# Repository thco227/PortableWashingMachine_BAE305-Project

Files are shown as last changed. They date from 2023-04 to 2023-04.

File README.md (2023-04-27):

# PortableWashingMachine_BAE305-Project
The following report contains the documentation of the construction of a portable washing machine for the class BAE 305. The members of this team were Maggie Barnes, Tiffany Coogle, Elyssa Roberts, and Hunter Walters.

## Summary
The goal of our project was to create a portable washing machine. The portable washing machine is applicable for situations in which the user has only a few small items of clothing to wash, and does not want to use a full size washing machine for them. Because of this, the portable washing machine that was created is most suitable for items such as socks, underwear, etc. The portable washing machine body is made from a 2 gallon bucket, and contains two pumps, a valve, a motor, and a 3D printed impeller. An Arduino RedBoard was used to control the operation of each component of the washing machine. The washing machine has three cycles: 1, 2, and 3 minutes, which each fill and drain twice to wash the clothes, remove the dirty water, then rinse. The user can select the desired cycle by inputting their selection into the serial monitor of the computer connected to the RedBoard. Then, when the user is ready, a switch can be used to start the cycle. At the end of the cycle, a buzzer beeps to notify the user to remove their clothes from the washing machine. Should the user need to stop the cycle before the specified duration, the switch can be used to stop the cycle midway. This project was initiated in January 2023 and progress was tracked using the Scrum project development method. The complete project was presented for assessment on April 20th, 2023, and all features on our project backlog were demonstrated successfully.



## Design Description 

### Materials
* 4 V23234-B1001-X004 Plug-in Mini ISO Relays
* 4 relay bases
* Jumper wires
* 3 TIP 31C Transistors
* 3 10k ohm resistors
* Arduino RedBoard
* Computer with Arduino IDE downloaded
* 1 Piezo Buzzer
* 1 Button
* 2 B07X9L5RNS HiLetgo DC Brushless Water Pumps (240L/min)
* 1 B08KS6FMC7 Gredia N/C DC Solenoid Valve
* 3/8" od. tubing
* LS-00086 OSEPP Electronics LTD DC Motor
* Global Specialties 100W Triple Output Switching DC Power Supply
* Female and Male Spade Connectors
* Crimper/wire stripper
* 2 Gallon Bucket with Lid
* 3D Printed Impeller
* 3D Printed Shaft Connector
* 1" od. PVC Pipe
* Hand Saw
* Kroger 1 Gallon Chocolate Ice Cream Bucket
* 1 set of Alligator Probes

### Design

#### Physical Design
When first creating the design for the washing machine, a five gallon bucket was the selected size for the unit. However, after calculating the torque needed to move that much water plus clothing and considering the voltage requirements and prices, a size reevaluation was necessary. A five gallon bucket half full of water was estimated at about 8 pounds without the weight of clothing. With a half foot of diameter estimated, around 4 lb-ft of torque would be needed at the minimum. The motors rated at this torque were very expensive and often required higher voltages. In the end, a 2 gallon bucket was decided on, with the intention to not fill it completely. Based on the size adjustment, a motor was chosen. The LS-00086 DC motor was chosen due to its low price, low voltage, and torque rating of 2.18 lb.-ft. The B07X9L5RNS brushless DC water pumps were chosen for their pumping capacity (240 L/min), low price, and low voltage/power consumption. Two were purchased: one to pump water in and one to empty the reservoir. In addition to these pumps, a B08KS6FMC7 Gredia normally closed DC solenoid valve was chosen to keep the unprimed outlet pump from continuing to send water into the drain.

Based on the size adjustment, a motor was chosen. The LS-00086 DC motor was chosen due to its low price, low voltage, and torque rating of 2.18 lb.-ft. The B07X9L5RNS brushless DC water pumps were chosen for their pumping capacity (240 L/min), low price, and low voltage/power consumption. Two were purchased: one to pump water in and one to empty the reservoir. In addition to these pumps, a B08KS6FMC7 Gredia normally closed DC solenoid valve was chosen to keep the unprimed outlet pump from continuing to send water into the drain.

#### Circuit Design
When designing the washing machine, an important factor was being able to control the operation of the pumps, motor, and valve, which all operated at 12 volts DC. This voltage could not be supplied from the RedBoard alone, so relays were used to switch them on and off. The components of the washing machine were connected to the switch connected terminals on the relay. A 12 volt supply was connected to these terminals as well. When the relay was turned on, the switch would close, allowing the 12 volts to flow to ground, and subsequently turning on the desired component. 

To turn the relay on and off, a controllable signal was needed on the non-switch connected terminals. However, the current needed to turn on the relay was calculated to be _ mA, which was too high for the RedBoard to produce. To achieve the desired current, transistors were used. The TIP31C models were used in the circuit. Four digital output pins (7, 8,12, and 13) from the RedBoard were connected to the bases of the transistors. A 12 volt supply was connected to the collector on the transistor. The emitter was connected to the relay. When the RedBoard sent out a 5 volt signal to the transistor, the 12 volts attached to the transistor would be allowed to flow through the relay to ground. This higher voltage was able to produce enough current to trigger the relay.

The design of the circuit also included a piezo buzzer and a switch. They were connected to the RedBoard via pins 5 and 2 respectively. When pin 5 sent out a signal, the buzzer would play a tone. Pin 2, which was connected to the switch, was set to input pullup mode. This meant that the pin would read zero until the switch was moved, then it would read low. The input pullup resistor mode was used to prevent floating values.  

To help make the schematic easier to read, the wires leading to ground are highlighted in red, the wires connected to power are highlighted in green, and the wires connected to a pin are various colors of blue.



#### Code

The code that operated the circuit was created in Arduino IDE and is explained below. First, the pins were set as constant integer variables as shown below.
```c
const int SpeakerPin = 5;

const int MotorPin = 7;

const int DrainPin = 8;

const int PumpPin = 12;

const int ValvePin = 11;

const int OnOffPin = 2;
```
The variable "CycleType" was initialized as a string so it could hold other strings. This was essential to allow the user's input to be read correctly.
```c
String CycleType;
```
The following variables set the time to run each component of the washing machine. A "long" variable type, which allows numbers from -2,147,483,648 to 2,147,483,647 to be assigned to it, was used. This allowed for a higher level of variability in the cycles. The times could be set to larger numbers than was possible with an integer variable, which only went from -32,768 to 32,767.
```c
long FillTime;

long SpinTime;

long DrainTime;

long ValveTime;
```
In the setup loop, the all pinmodes except the switch pin were set to output. These pins needed to output HIGH to activate the transistors.
```c
void setup() {

pinMode(SpeakerPin, OUTPUT);

pinMode(MotorPin, OUTPUT);

pinMode(DrainPin, OUTPUT);

pinMode(PumpPin, OUTPUT);

pinMode(ValvePin, OUTPUT);
```
The switch pin was set to input pullup. This allowed the switch to ground a signal when connected.
```c
pinMode(OnOffPin, INPUT_PULLUP);
```
In this loop, serial connection was created by using the Serial.begin command and setting the baud rate to 9600.
```c
Serial.begin(9600);
```
Finally, the setup loop was concluded by displaying a message to prompt user input to choose a cycle type and instructing the user how to use the switch.
```c
Serial.println("Push switch towards resistor side before inputing cycle type if ready to start cycle. 
During the cycle push the switch away from the resistor if you would like the cycle to end.");

Serial.println("Choose cycle: Light, Normal, Heavy");

Serial.println("L = Light, N = Normal, H = Heavy");
}
```
The main loop was comprised of many if and else statements. The blanketing if statement told the program to start if the user input something into the serial monitor. 
```c
void loop() 
{
if (Serial.available() > 0)
```
The string variable "CycleType" stored the input until "\n" was found, which equated to the user pressing the enter key. Depending on the user input, three different if or else if statements could be triggered. These three loops had varying messages and times to correspond with the cycle type. The light cycle is shown below, however the normal and heavy cycles have the exact same code, except with the time variables set to different times and the messages displaying the corresponding cycle. Note that the times are given in milliseconds.
```c
CycleType = Serial.readStringUntil('\n');

if (CycleType == "L")

Serial.print("You have chosen LIGHT.");

FillTime = 15000;

DrainTime = 30000;

SpinTime = 5000;
```
To easily adjust and call upon the major actions of the washing machine, functions were created. Fill, drain, valve, and motor functions were comprised of turning the corresponding pin to high, delaying for a set time, and then turning the pin to low. By setting the time in each function to a variable, the times for each cycle type could be easily adjusted. Each cycle type redefined the times for each function to allow to customize the intensity. The fill function is shown below, however the other functions follow a similar outline, with different pins being set to HIGH.

```c
void fill(){

  digitalWrite(MotorPin, LOW);
  
  digitalWrite(ValvePin, LOW);
  
  digitalWrite(DrainPin, LOW);

  digitalWrite(PumpPin, HIGH);
  
  delay(FillTime);

  digitalWrite(PumpPin, LOW); }
  ```

In each cycle, after the times were defined, the same sequence code would run. The sequence called on various functions created to fill, spin, drain, and turn the valve on and off. Before inputing a cycle type into the serial monitor, the user would be prompted to turn the switch toward the resistor on the breadboard if they were ready to start the cycle. With the switch toward the resistor, the pin would read LOW. When the switch was pressed away from the resistor, the pin would read zero. The code used this to create a system in which the cycle could be stopped in the middle. This was accomplished by putting an if statement before each step of the cycle. When the switch was pushed toward the resistor, it would read LOW, and would allow the code to run. If pressed away, the pin would read zero, and the code would stop because the conditions would not be fulfilled.
```c
if (digitalRead(OnOffPin)==LOW) fill();

if (digitalRead(OnOffPin)==LOW) spin();

if (digitalRead(OnOffPin)==LOW) drain();

if (digitalRead(OnOffPin)==LOW) fill();
```
A function for the beep at the end of the cycle was also created, which included the tone command so the pin, frequency, and duration could be selected. This function was not put within an if statement on the condition of the switch, so the user would know if their cycle had ended had they decided to end it midway.

```c
void StopBeep() {
  digitalWrite(MotorPin, LOW);
  
  digitalWrite(ValvePin, LOW);
  
  digitalWrite(DrainPin, LOW);
  
  digitalWrite(PumpPin, LOW);

  tone(SpeakerPin, 500, 1000);
}
```

#### 3D Printing Design
For the inner workings of the machine, we researched actual appliances. Commercially available washing machines most often employ one of two washing methods: agitation or impeller washing. In an agitation washing machine, a central shaft with vanes rotates to spin clothes in water and wash them. An impeller is a low disc with fins that sits at the bottom of the basket, and impeller washing uses this structure to wash clothes. The design takes advantage of the friction generated between the articles of clothing to wash them and uses less water than an agitation machine does. For our small scale machine, we wanted to optimize our water use, so the impeller design was the ideal choice. When we took into consideration the materials we would be using, we realized it would be far easier to 3D print an impeller than a central agitator.

Our impeller design is simple: it's a flat disc that rises in the center to form a low cone. This center is hollow to allow our central shaft, a PVC pipe with an outer diameter of approximately 1 in, to be inserted. From the center cone, eight identical vanes protrude, lofting down to meet the edge of the disc. Commercial impellers tend to have six of these vanes, but we chose to use either for a more sturdy impeller, as, at the time of designing this part, we were unsure how much stress the impeller would be under. Future iterations of this project should test different impeller designs. The eight-vaned impeller part file is shown below.

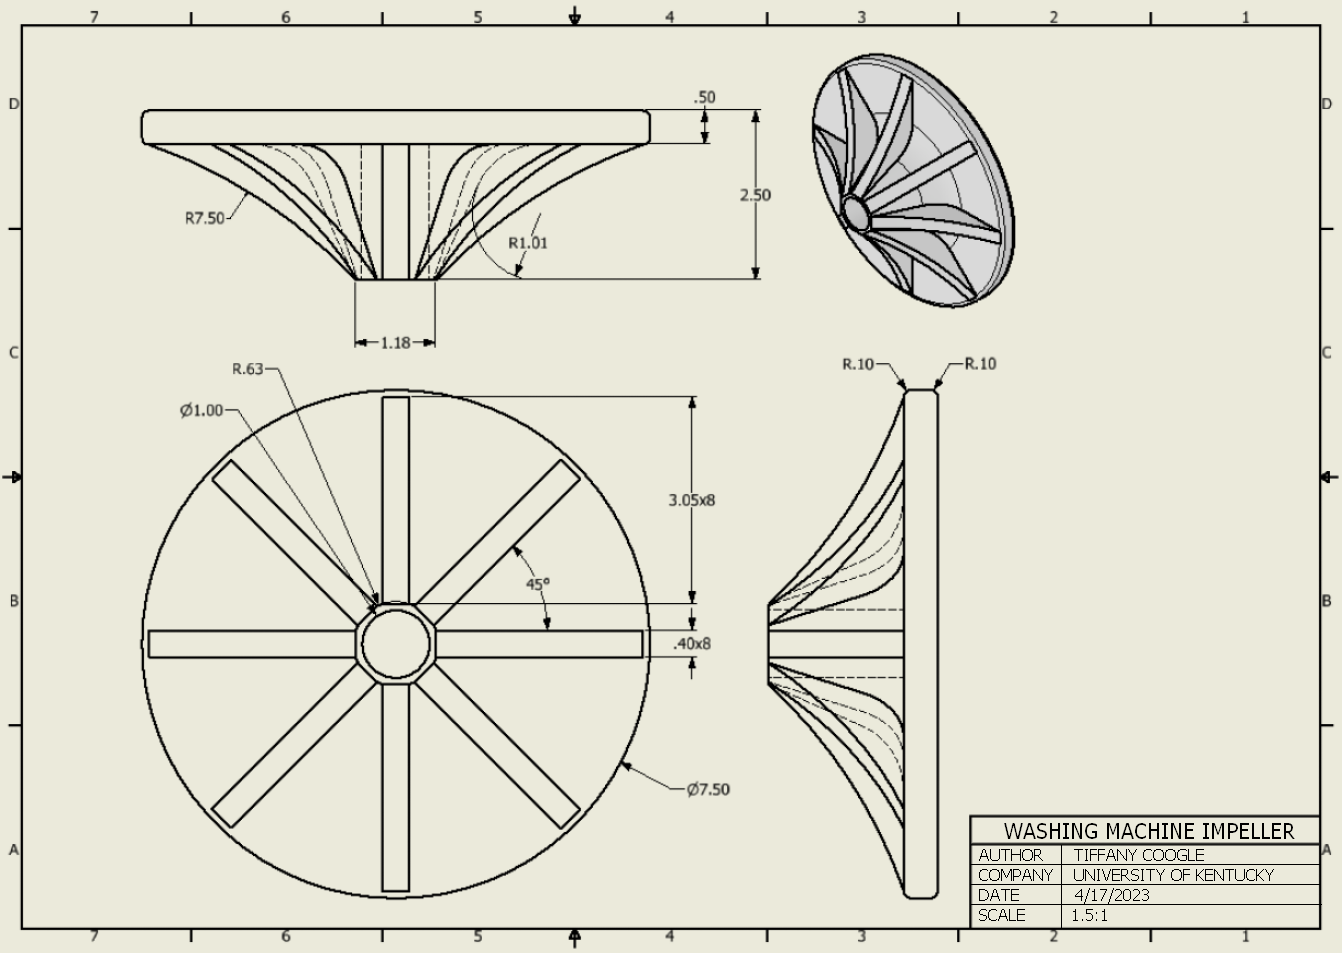
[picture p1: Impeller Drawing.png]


To create this part, we used the 3D printers available at the Innovation Center at the University of Kentucky. The printer used was the Prusa Mini+, printing with Inland 1.75mm PLA filament. This printer's print bed is a 7 in square, which is just smaller than the impeller's diameter of 7.5 in. To use the Prusa Mini+, we cut our impeller file into four identical parts, as in the drawing file below. These four parts each had a mass of 40.01 grams, resulting in a total combined mass of 164.04 grams. 

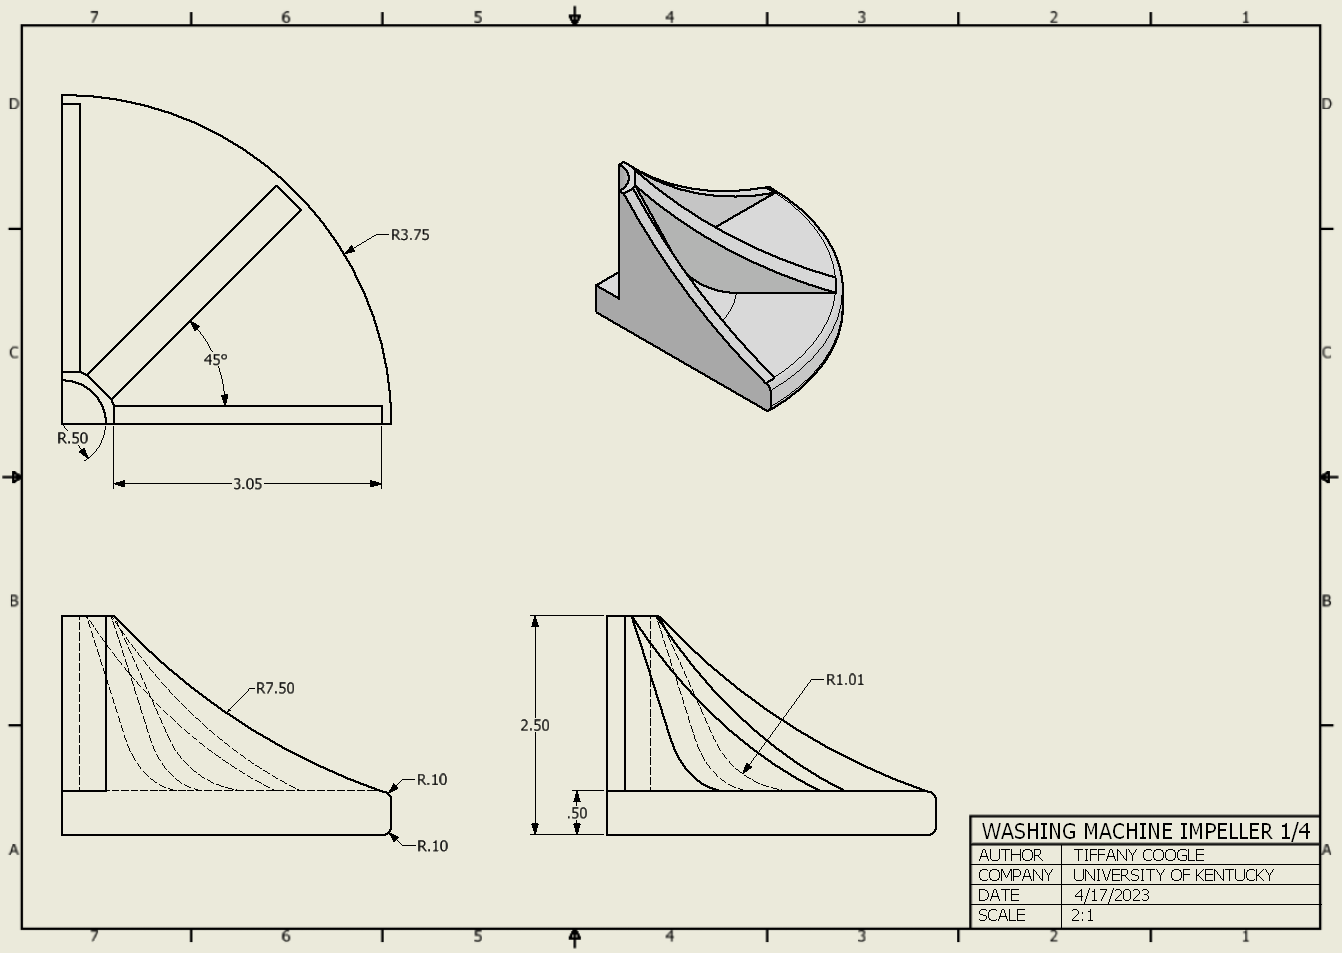
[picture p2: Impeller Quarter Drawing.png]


Once these were printed, the triangular faces were glued together using E6000 industrial adhesive to form the full impeller, as shown in this photograph.

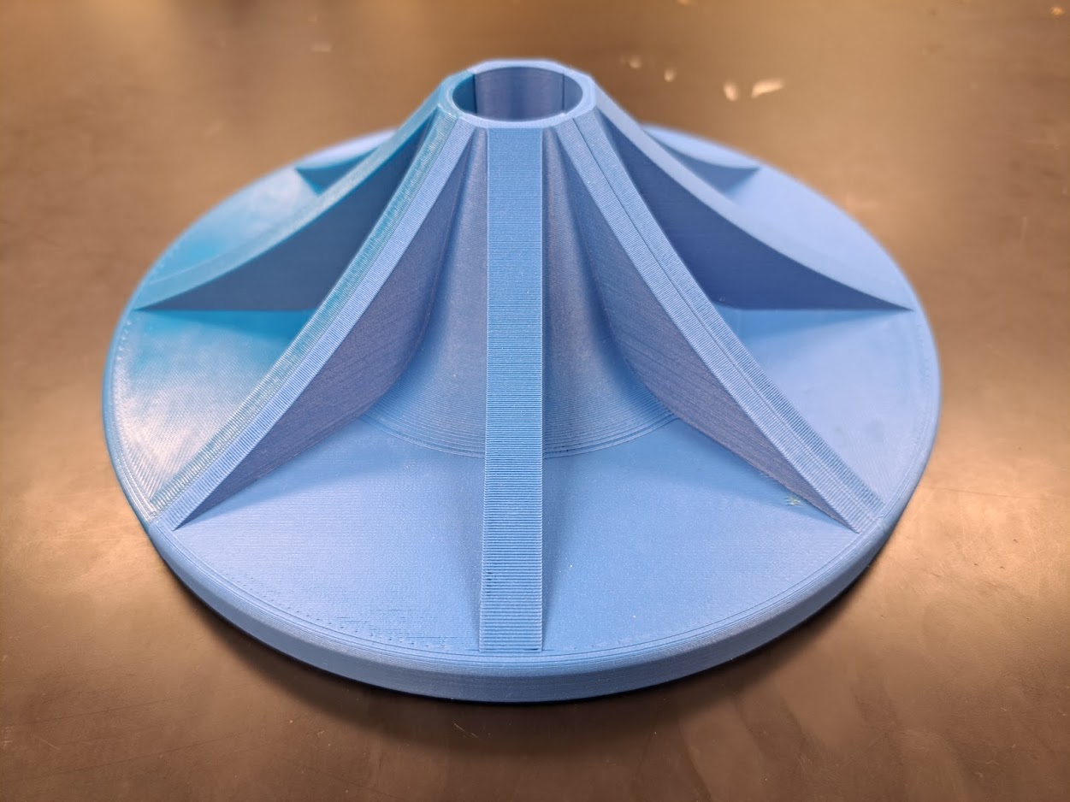
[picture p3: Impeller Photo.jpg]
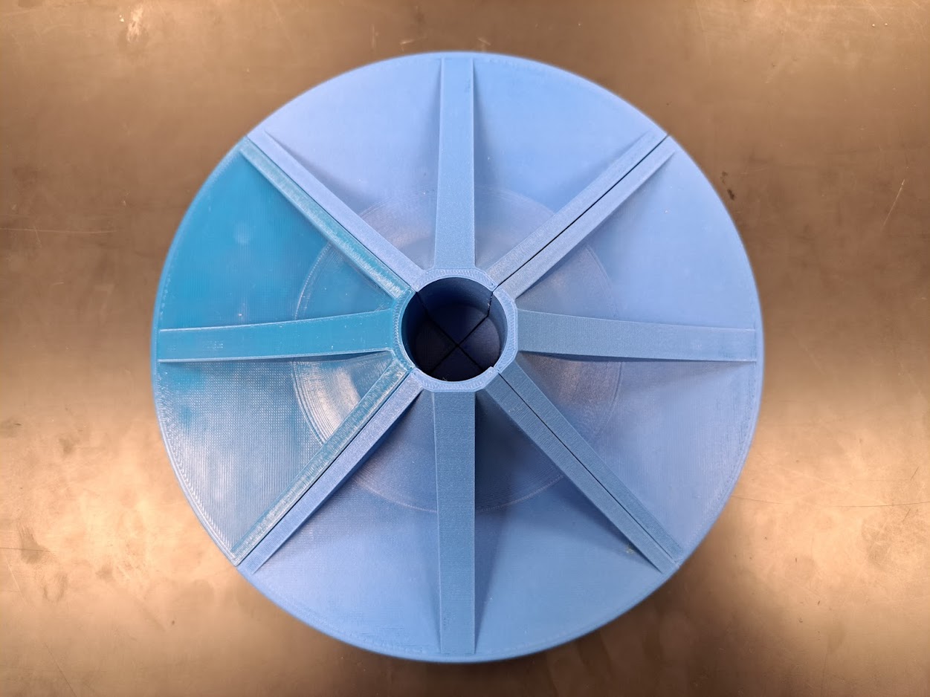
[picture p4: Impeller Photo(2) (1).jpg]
 

Another key component of the physical washing system is the motor mount. As mentioned previously, we chose to use a section of PVC pipe as a central shaft that would connect our impeller to the motor. To rotate this shaft from the motor key, we designed a fitting for the end of the pipe that has a hole to insert the motor shaft. This part was printed using the Prusa Mini+, with Inland 1.75mm PLA. The total mass of the print was 13.18 grams. The images show our drawing file and photos of the final print.

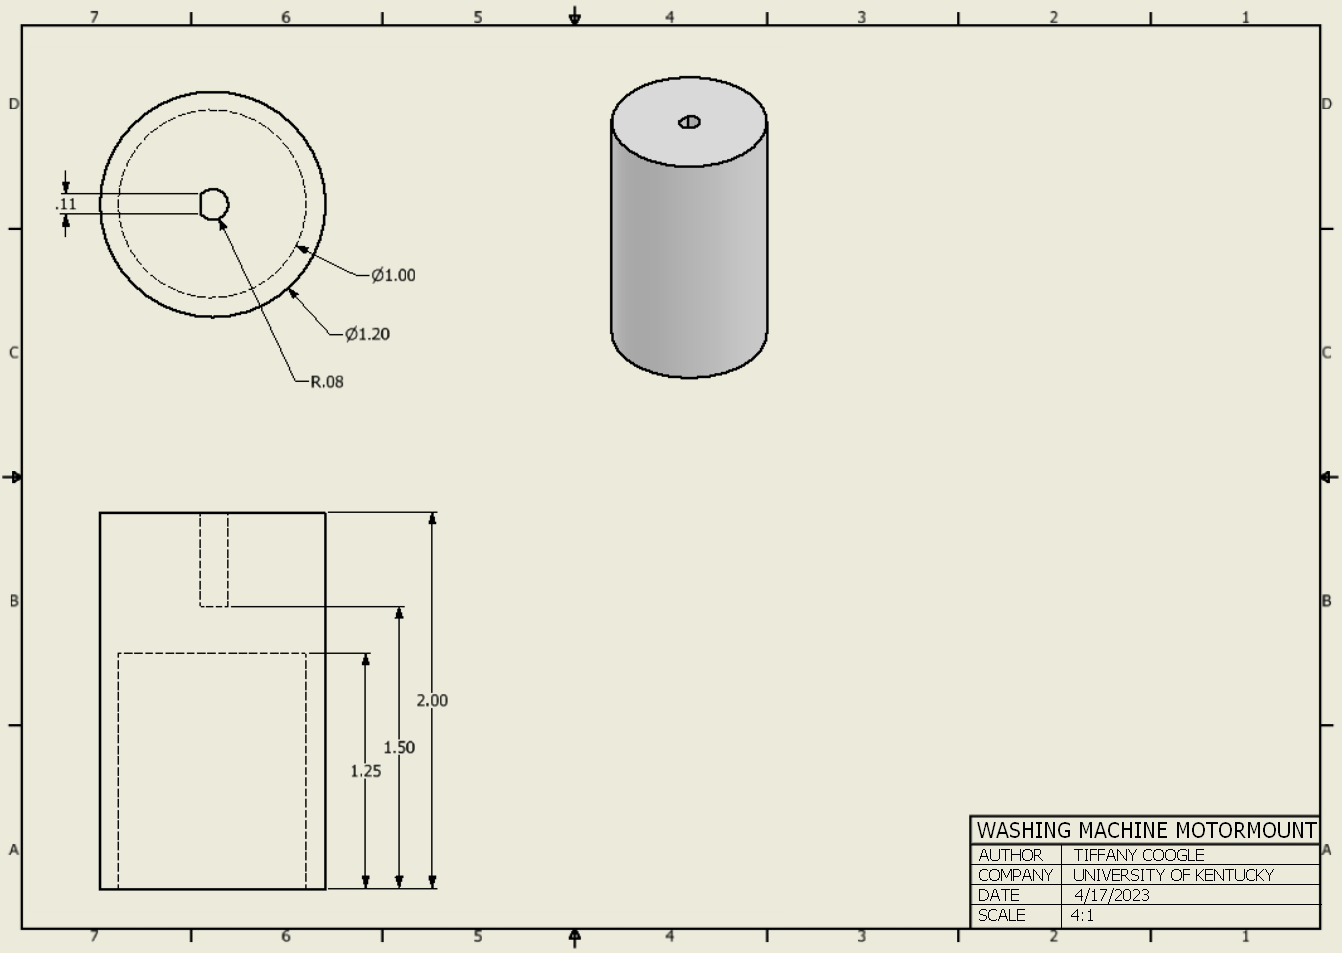
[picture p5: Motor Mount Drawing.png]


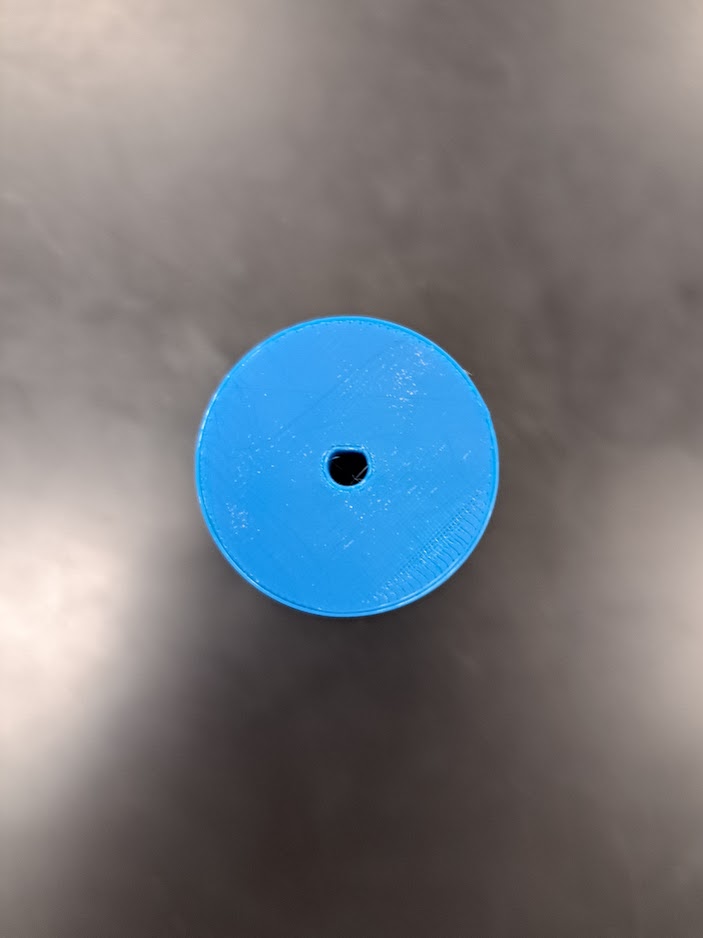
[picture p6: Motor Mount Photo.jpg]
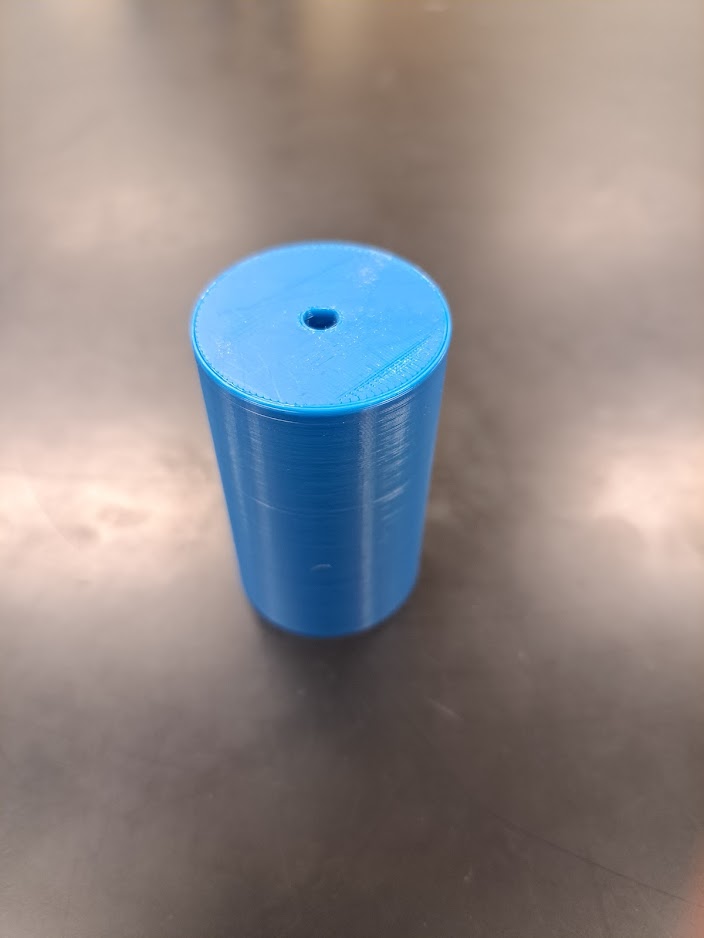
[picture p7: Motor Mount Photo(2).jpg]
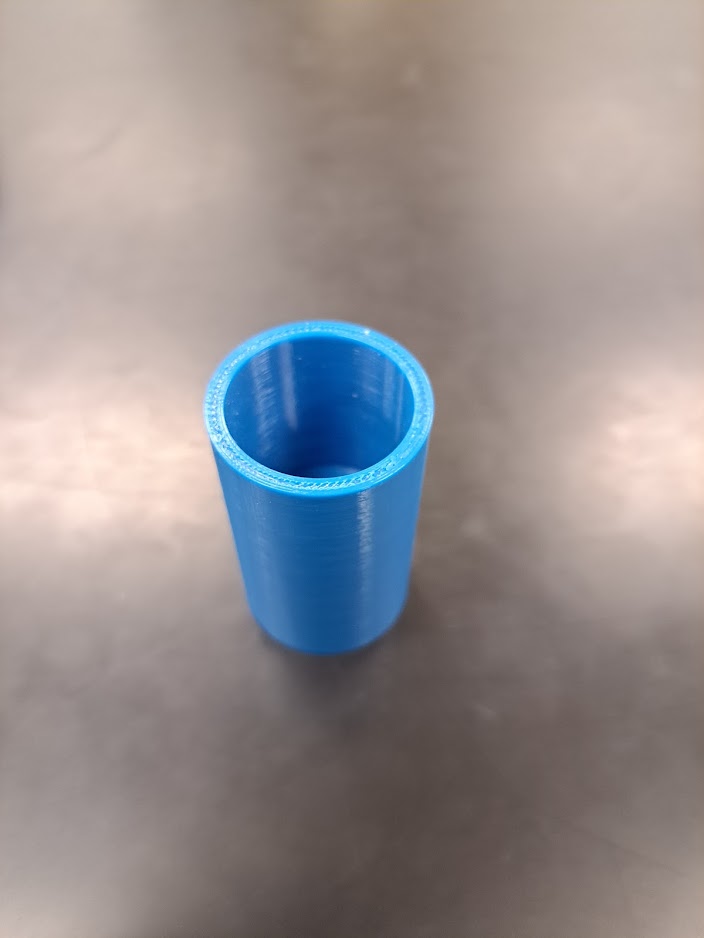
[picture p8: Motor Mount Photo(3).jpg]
  

#### Laser Cut Design

The initial plan for the stand that would hold the bucket up was to 3D print. With the design having a diameter right above 9 inches, an industrial size printer would have been needed to perform the print. Then considering a new way to print smaller pieces and glue them together, the cost and time to do so was still not reasonable. The final solution was to laser cut 4 (dimensions) pieces, 1 base piece that was (dimensions) with a circle cut out in the middle, and 8 (dimensions) to create legs so that the bucket would be lifted. The circle cut out of the bottom and the legs being added so the bucket was 4 inches off the surface, was to supply room for the motor to be mounted. These components were laser cut from a 11.5 x 23.5 x .25 inch thick piece of wood. When laser cut, divots were added to the edges of the components to help them be glued together with more ease and stability. Gorilla wood glue was used to hold the pieces together.
 
!!!!!PICTURE OF PEICES LASER CUT WITH LABELED DIMENSIONS!!!!!

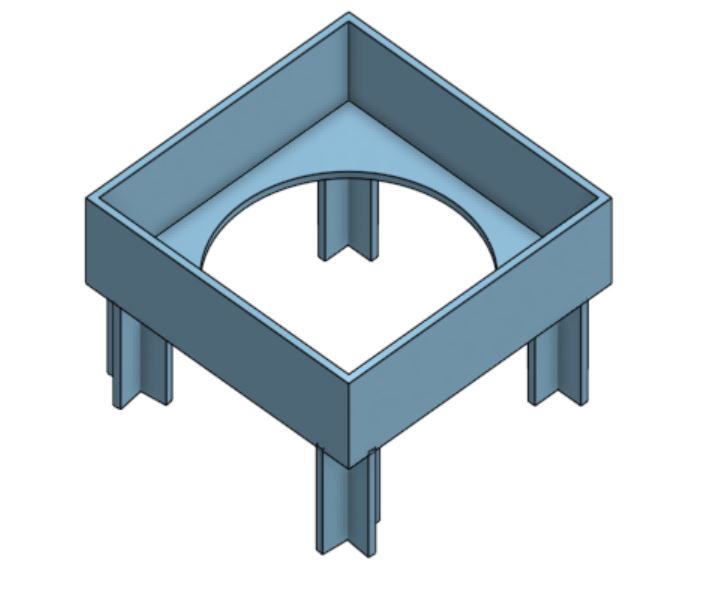
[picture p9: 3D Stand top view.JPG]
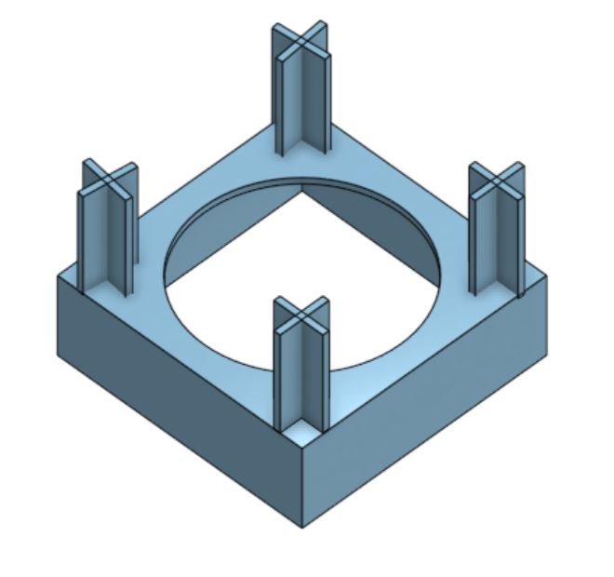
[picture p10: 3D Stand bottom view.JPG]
 

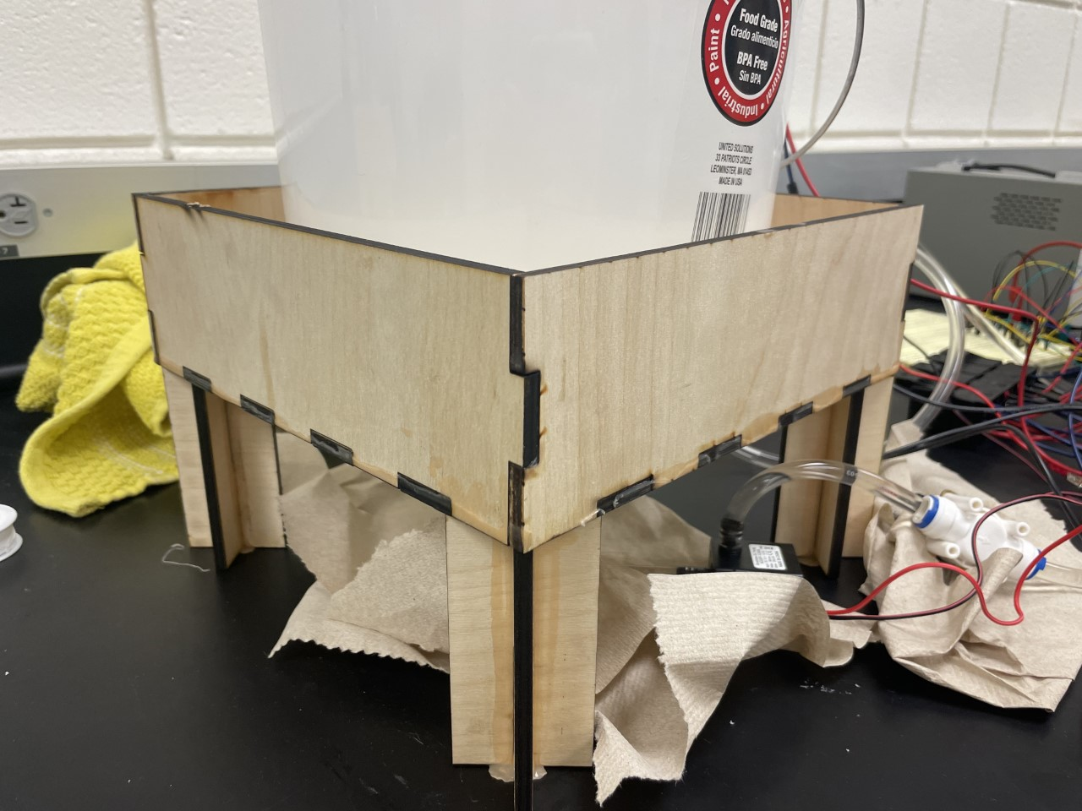
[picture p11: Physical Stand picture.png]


## Testing

#### Construction

During the construction of the initial circuit, the position of the relay relative to the transistor was adjusted. At first, the relay was positioned directly after the voltage supply and before the emitter. However, the relay caused a voltage drop before the transistor which was so low, that the voltage difference did not allow current to flow from the power supply to ground. To fix this, the relay was repositioned after the emitter and before the ground. 

#### Pump Flow Rate Testing
The timing of the drain and pump were important in ensuring the washing machine completed a full cycle. The pumps were advertised as having a flow rate of 240L/hr. To test the flow rate, the pumps were set to run for a given amount of time, and the water was collected in a graduated cylinder. The testing resulted in a flow rate of about 140 L/hr. This reduction in flow rate was most likely due to the tubing attached to the pump, causing the water to slow. 

#### Cycle Testing
To run the entire cycle, the water needed to end at the same level that it started at. We trouble shooted this issue by running the drain and fill functions for different amounts of time. We found that the drain time needed to be roughly double the fill time.

## Design Results Discussion
After completing the project, if we wanted to improve the washing machine to be a fully functional we would do the following. The circuitry would need to be contained and a battery pack could be used as opposed to a DC power supply. We would also include a level sensor to ensure that when the off switch was flipped, the reservoir would be completely drained for the next user. 

## Test Results Discussion

#### Motor
To test the motor that controlled the agitator we ran just that part of the code to confirm the motor would spin the agitator correctly. After running the code we could confirm the motor was indeed working correctly at an efficient speed.

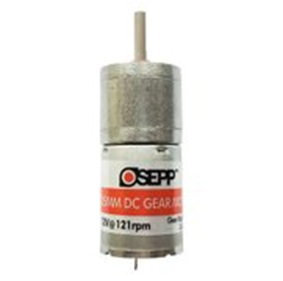
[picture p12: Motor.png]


#### Pumping System
To test the pumping system we connected tubing to the pumps and filled one bucket with water. The tubes ran from the bucket with water to the main system, and back to the bucket of water. When testing we ran our code and were able to confirm that the pumps and tubing system were indeed able to take water from the water bucket, fill the main system, then empty the main system back to the water bucket.

Pump Testing Data
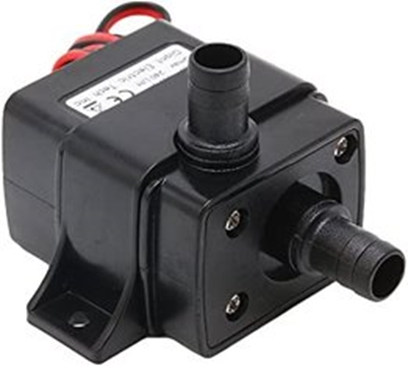
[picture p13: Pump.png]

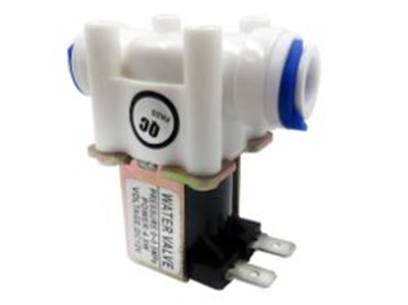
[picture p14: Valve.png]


#### Buzzer
To test the buzzer system that goes off at the end of each cycle, we ran all three types of cycles and made sure the buzzer successfully went off at the end of each one.

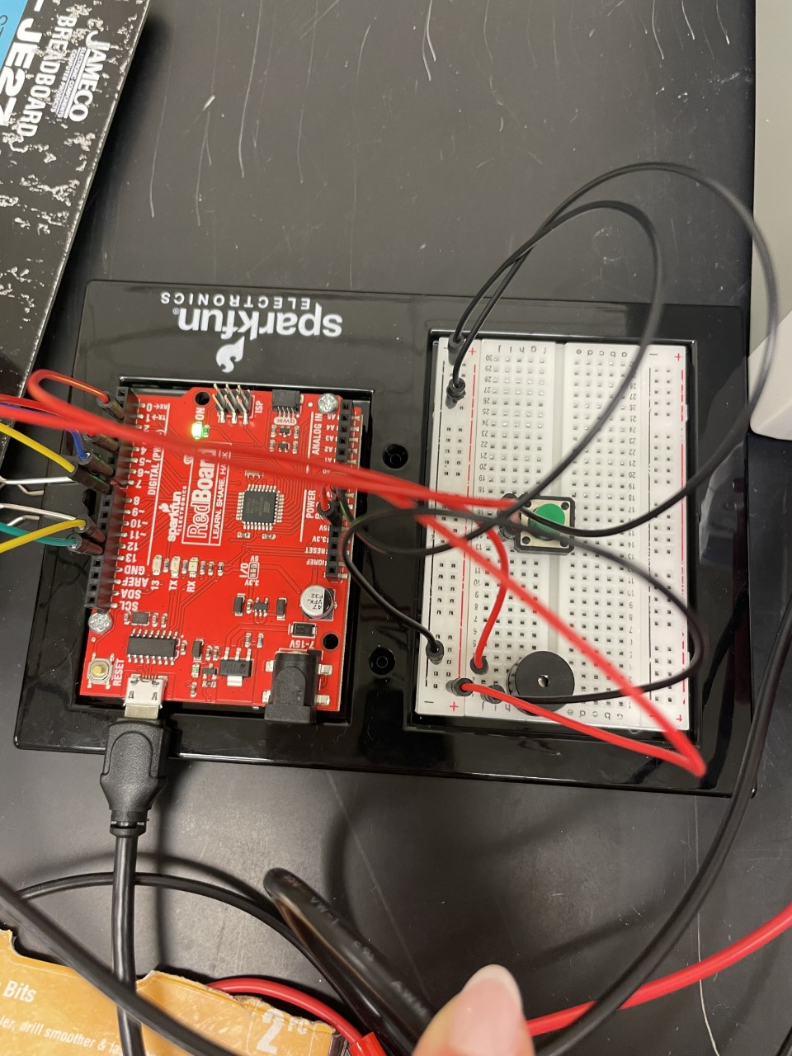
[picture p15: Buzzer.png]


#### Physical Components 
To test to make sure all of our physical components worked together, we had to bring all of the parts of the project into the lab and put it together. After assembling we were able to confirm all the pieces fit together. Once getting all the pieces fitted together properly we ran a full cycle to make sure everything ran smoothly. The cycle was ran and completed successfully.


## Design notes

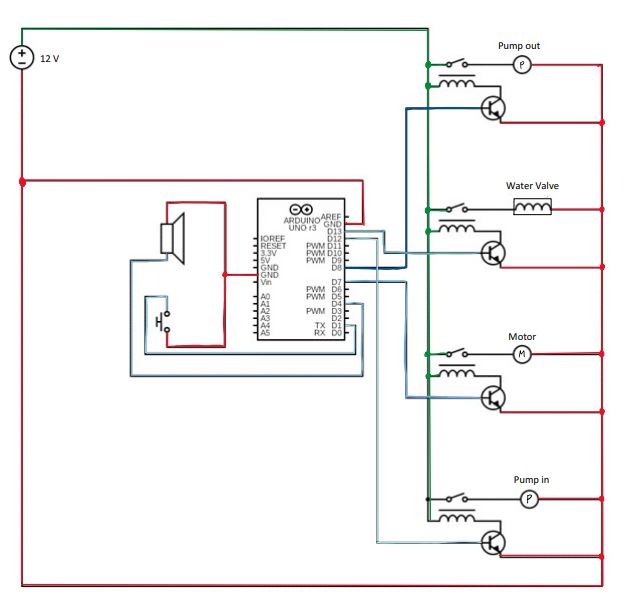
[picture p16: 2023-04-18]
BAE 305 Project schematic.JPG

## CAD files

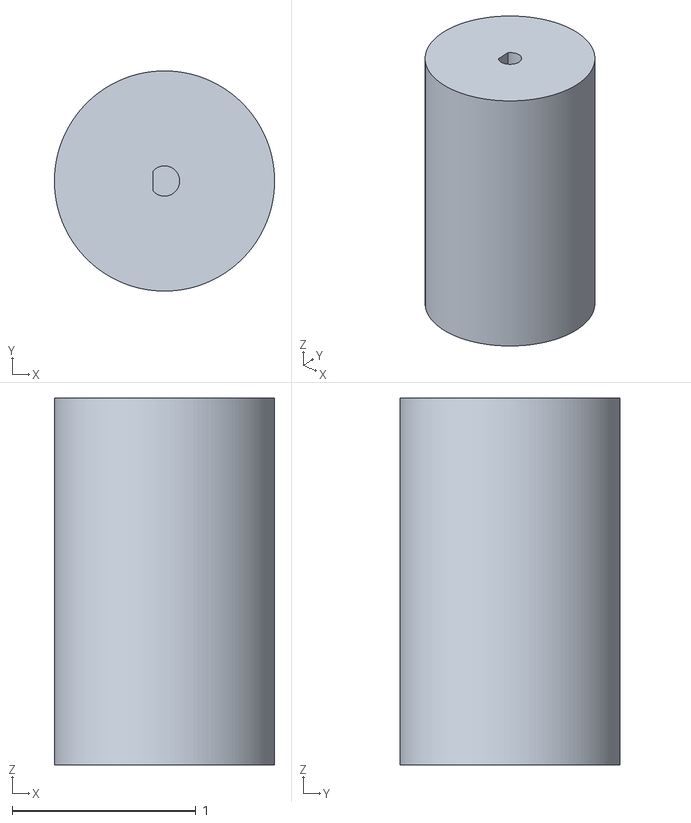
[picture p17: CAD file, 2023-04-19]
Motor Mount .165in.stl
1.20 x 1.20 x 2.00

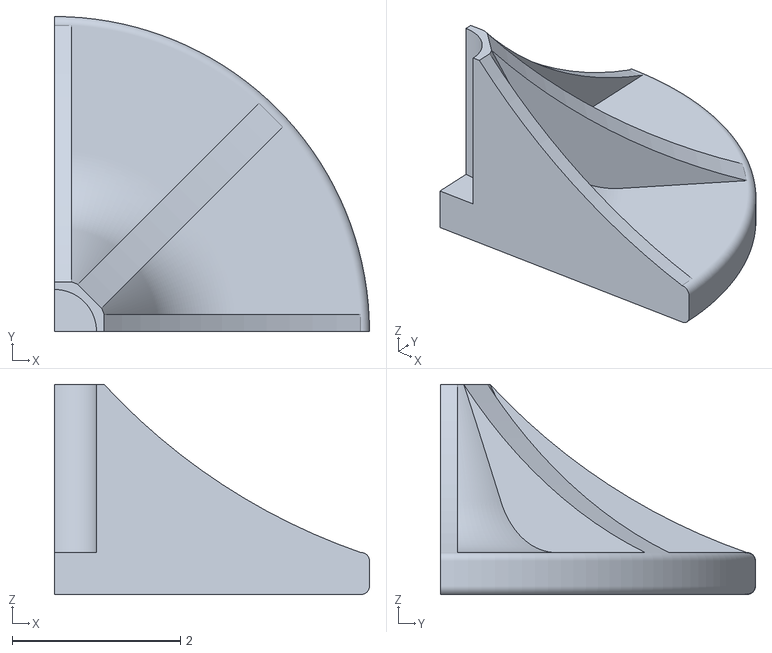
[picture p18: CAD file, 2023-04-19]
Impeller 7.5in quarter.stl
3.75 x 3.75 x 2.50

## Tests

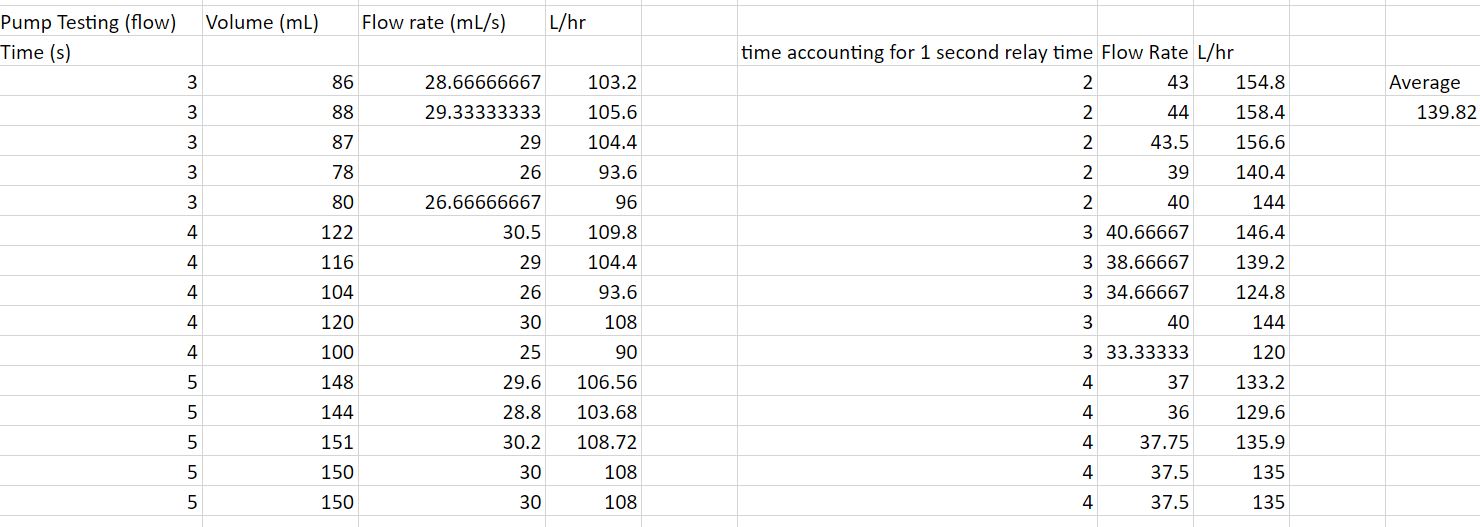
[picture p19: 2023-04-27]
Pump Testing Data.JPG

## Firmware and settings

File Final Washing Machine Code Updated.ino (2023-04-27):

// PIN SETUP

//Piezo buzzer pin
const int SpeakerPin = 5;  

//Set up relay pins for each component
const int MotorPin = 7;
const int DrainPin = 8;
const int PumpPin = 12;
const int ValvePin = 11;

//Set up on/off switch pin
const int OnOffPin = 2;

//Set the variable to a string type
String CycleType;

//create variables for time to run components
long FillTime;
long SpinTime;
long DrainTime;
long ValveTime;


//FILL FUNCTION
void fill(){

  //Make sure other components are off
  digitalWrite(MotorPin, LOW);
  digitalWrite(ValvePin, LOW);
  digitalWrite(DrainPin, LOW);

  //Turn on pump
  digitalWrite(PumpPin, HIGH); 

  //Keep the pump on for x seconds 
  delay(FillTime);

  //Turn off pump
  digitalWrite(PumpPin, LOW);
}


//DRAIN FUNCTION
void drain(){

  //Make sure other components are off
  digitalWrite(MotorPin, LOW);
  digitalWrite(PumpPin, LOW);

  //Open valve so water can flow through
  digitalWrite(ValvePin, HIGH);

  //Turn on drain pump
  digitalWrite(DrainPin, HIGH); 

  //Keep the drain on for X seconds 
  delay(DrainTime);

  //Turn off drain and close valve
  digitalWrite(DrainPin, LOW);
  digitalWrite(ValvePin, LOW);
}


//SPIN FUNCTION
void spin(){
  
  //Make sure other components are off
  digitalWrite(PumpPin, LOW);
  digitalWrite(ValvePin, LOW);
  digitalWrite(DrainPin, LOW);

  //Turn on motor
      digitalWrite(MotorPin, HIGH);

      //Keep motor on for X seconds
      delay(SpinTime);

      //Turn off motor
      digitalWrite(MotorPin, LOW);
}


//END FUNCTION
void StopBeep() {

  //Set all pins to LOW
  digitalWrite(MotorPin, LOW);
  digitalWrite(ValvePin, LOW);
  digitalWrite(DrainPin, LOW);
  digitalWrite(PumpPin, LOW);

  //Have buzzer play tone to signify end of cycle
  tone(SpeakerPin, 500, 1000);
}

//SET PIN MODES 
void setup() {

//Set pizeo speaker pin to output
pinMode(SpeakerPin, OUTPUT);

//Set the relay pins to output
pinMode(MotorPin, OUTPUT);
pinMode(DrainPin, OUTPUT);
pinMode(PumpPin, OUTPUT);
pinMode(ValvePin, OUTPUT);

//Switch the on/off button to input pullup and set to input pullup, when switch is pushed away from resistor it reads LOW
  pinMode(OnOffPin, INPUT_PULLUP);

//connect with computer
Serial.begin(9600); 

//Prompt the user to input a cycle type, instruct user on how to use switch
Serial.println("Push switch towards resistor side before inputing cycle type if ready to start cycle. During the cycle push the switch away from the resistor if you would like the cycle to end.");
Serial.println("Choose cycle: Light, Normal, Heavy");
Serial.println("L = Light, N = Normal, H = Heavy");
}



//BEGIN 
void loop() 
{
  
  //If user types something
  if (Serial.available() > 0) 
  { 
    

    //Read string input until enter is pressed
    CycleType = Serial.readStringUntil('\n'); 

    //If user types L for light, this runs
    if (CycleType == "L")
    {
      //Print user's choice on serial monitor
      Serial.print("You have chosen LIGHT.");
      
      //Set the fill and draintime to 30 and 29 seconds, set spin time to 30 seconds
      FillTime = 15000;
      DrainTime = 30000;
      SpinTime = 5000;

    

      //Actual cycle: fills, spins, then drains twice, if the switch reads low at anytime, the current function finishes and then the whole cycle ends.
      if (digitalRead(OnOffPin)==LOW) fill();
      if (digitalRead(OnOffPin)==LOW) spin();
      if (digitalRead(OnOffPin)==LOW) drain();
      if (digitalRead(OnOffPin)==LOW) fill();
      if (digitalRead(OnOffPin)==LOW) spin();
      if (digitalRead(OnOffPin)==LOW) drain();

      //cycle is done so it beeps
      StopBeep();
      

    }

    //If user types N for normal, this runs
    else if (CycleType == "N")
    {
      //Print user's choice
      Serial.print("You have chosen MEDIUM.");

      //Set the fill and draintime to 30 and 29 seconds, set spin time to 45 seconds
      FillTime = 15000;
      DrainTime = 30000;
      SpinTime = 10000;

    

      //Actual cycle: fills, spins, then drains twice, if the switch reads low at anytime, the current function finishes and then the whole cycle ends.
      if (digitalRead(OnOffPin)==LOW) fill();
      if (digitalRead(OnOffPin)==LOW) spin();
      if (digitalRead(OnOffPin)==LOW) drain();
      if (digitalRead(OnOffPin)==LOW) fill();
      if (digitalRead(OnOffPin)==LOW) spin();
      if (digitalRead(OnOffPin)==LOW) drain();

      //cycle is done so it beeps
      StopBeep();
      
    }
    
    //If user types H for Heavy, this runs.
    else if (CycleType == "H")
    {
      //Print user's choice
      Serial.print("You have chosen HEAVY.");

      //Set the fill and draintime to 30 and 29 seconds, set spin time to 60 seconds
      FillTime = 15000;
      DrainTime = 30000;
      SpinTime = 15000;


      //Actual cycle: fills, spins, then drains twice
      if (digitalRead(OnOffPin)==LOW) fill();
      if (digitalRead(OnOffPin)==LOW) spin();
      if (digitalRead(OnOffPin)==LOW) drain();
      if (digitalRead(OnOffPin)==LOW) fill();
      if (digitalRead(OnOffPin)==LOW) spin();
      if (digitalRead(OnOffPin)==LOW) drain();

      //cycle is done so it beeps
      StopBeep();
           
    }
  }

}
